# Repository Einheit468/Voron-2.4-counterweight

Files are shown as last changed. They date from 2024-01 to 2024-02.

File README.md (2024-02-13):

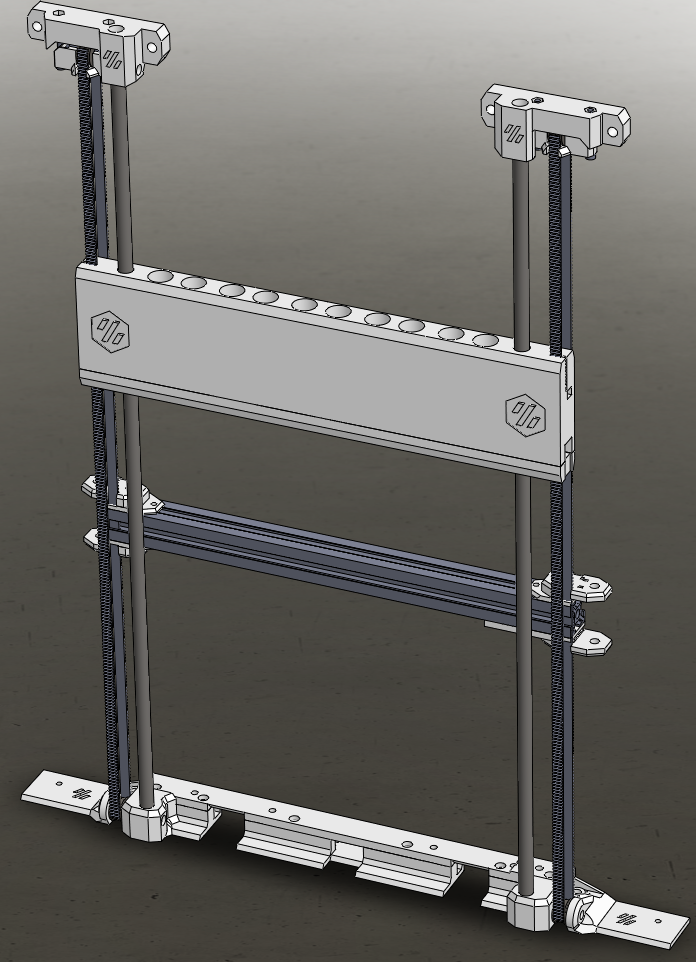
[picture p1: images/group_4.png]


The project is currently intended exclusively for __Voron 2.4 350mm__. <br>
The counterweight relieves the load on the rear Z stepper motors.<br>
Possible sagging of the gantry is also reduced.<br>

The disadvantage is that the acceleration force and braking force are increased.<br>
<br>
<br>

> [!WARNING]
> __I noticed that during input shaping the vibrations start to rattle due to the play in the counterweight bearing.
> Still looking for a solution to the problem.__

<br>
<br>
<br>
<br>

> [!WARNING]
> __The project is not yet fully completed.__ <br>
> - the building instructions are work-in-progess. <br>
> - some pictures are still old versions. <br>
> <br>
> But the parts and BOM are functional. <br>

> [!IMPORTANT]
> The __Z-cable chain__ must/should be exchanged for one of the narrower __X or Y cable chain__.

> [!IMPORTANT]
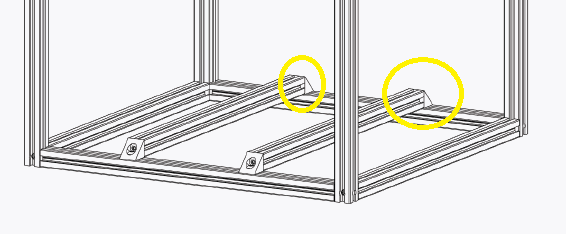
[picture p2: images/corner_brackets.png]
>  <br>
> The __corner brackets__ should also be attached to the ends of the heated bed bracket on the frame.

### Required Hardware:<br>
* List of Hardware: [BOM](/BOM.md)

### Build guide:<br>
* [Build](/Build.md)

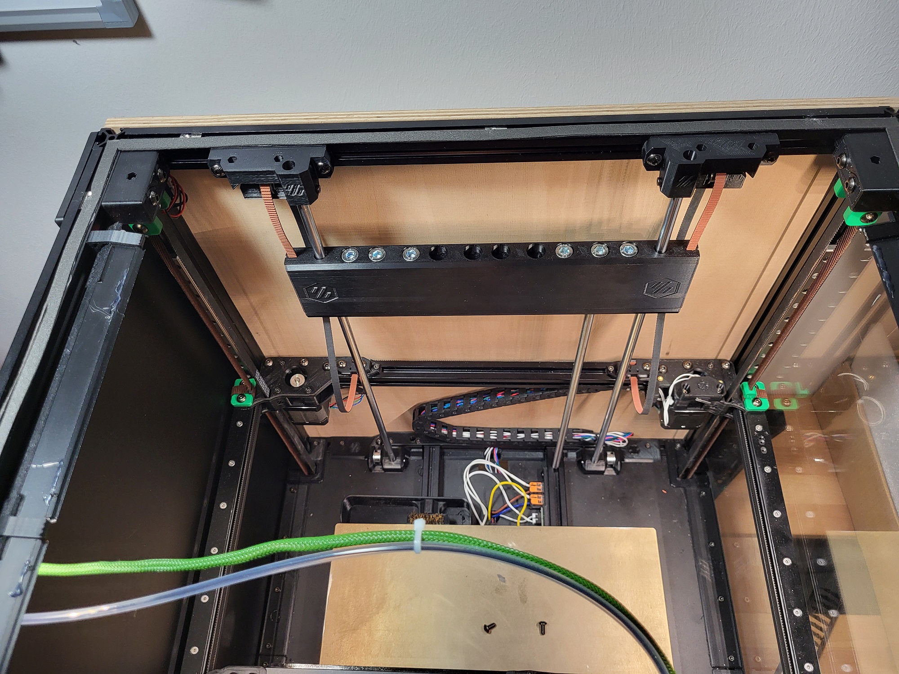
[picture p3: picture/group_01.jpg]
 <br>
_The weight is intentionally relaxed in the picture.
The lower strap is not mounted._

# Changelog

* 10.02.2024: modified the belt tension on  the gantry side. It wasn't aligned with the timing belts. <br> also added cable tie holders for timing belts and cables. <br>
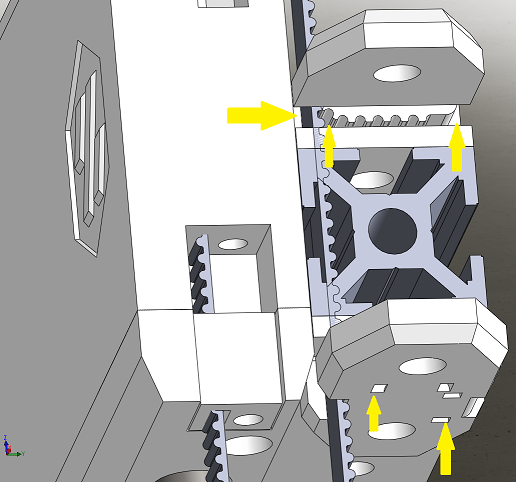
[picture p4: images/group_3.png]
  <br>
* 12.02.2024: Distance increased by 0.5mm between gantry and counterweight. <br> Because he sanded minimally.
<br>
<br>

# Special Thanks to
__spitzbirne32__

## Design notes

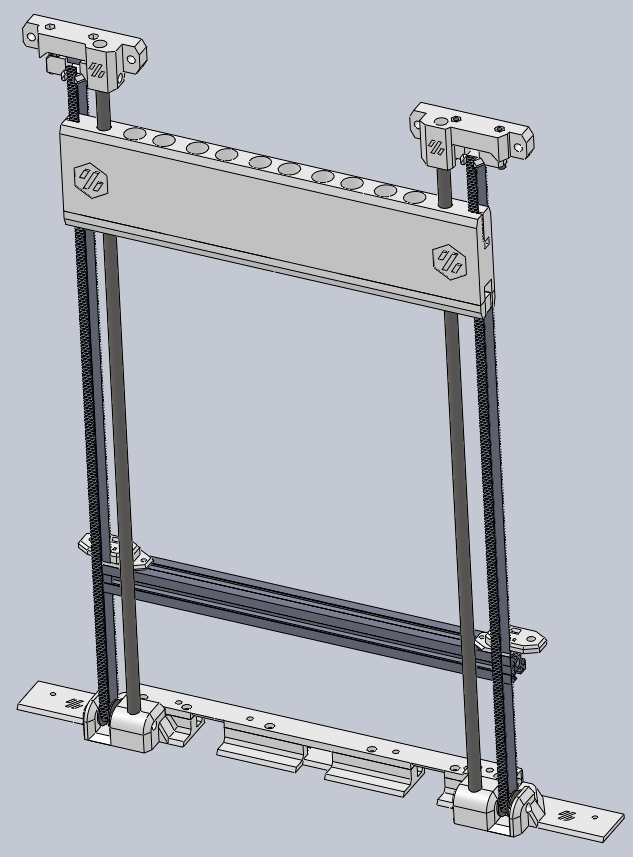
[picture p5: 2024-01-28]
images/group_1.png

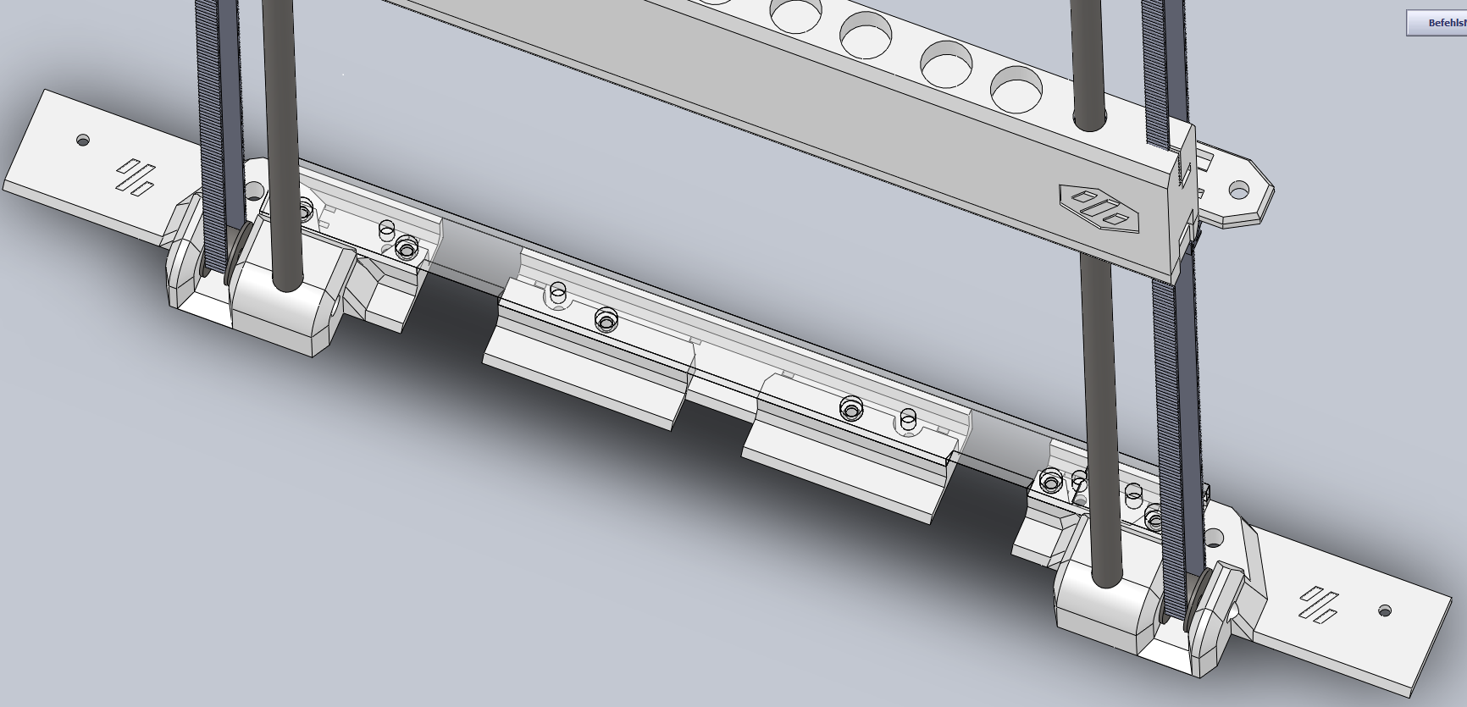
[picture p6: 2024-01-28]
images/beldholder_down_4.png

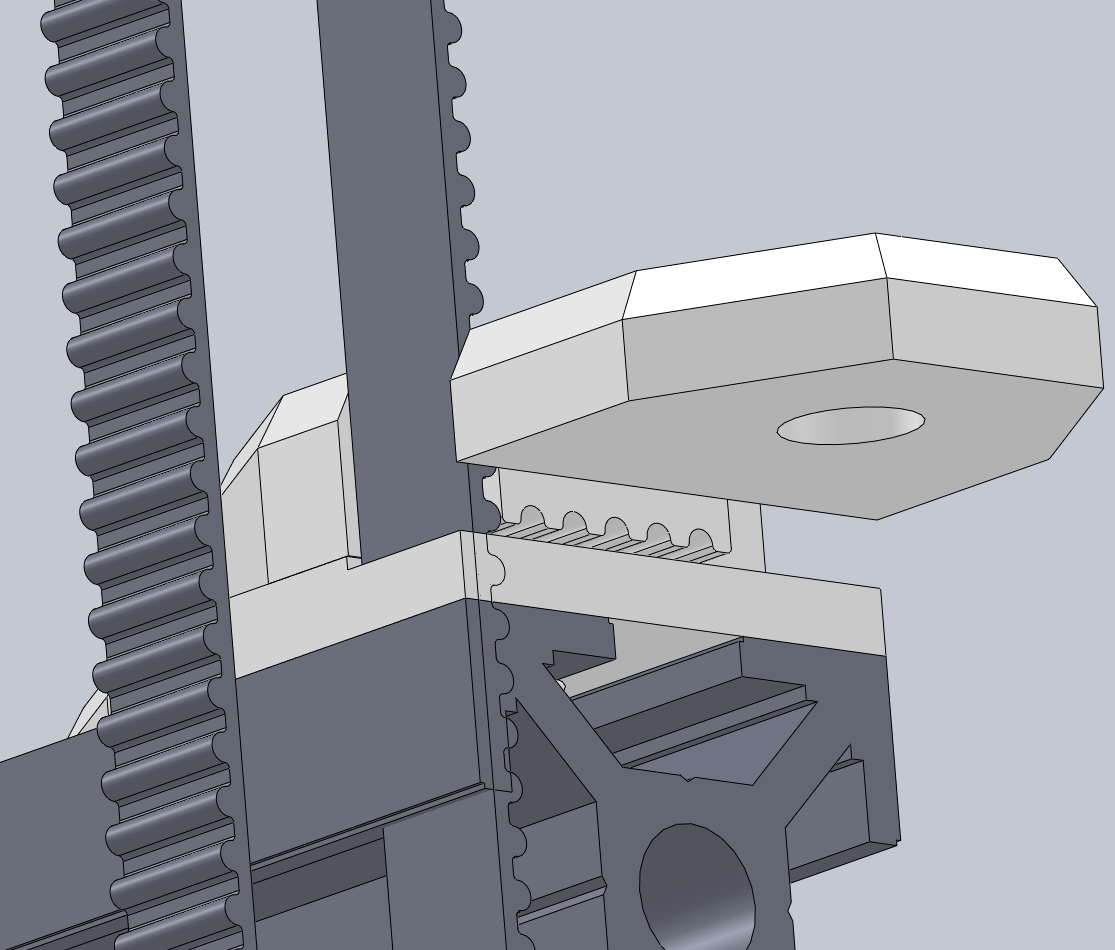
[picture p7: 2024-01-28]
images/gantry_2.png

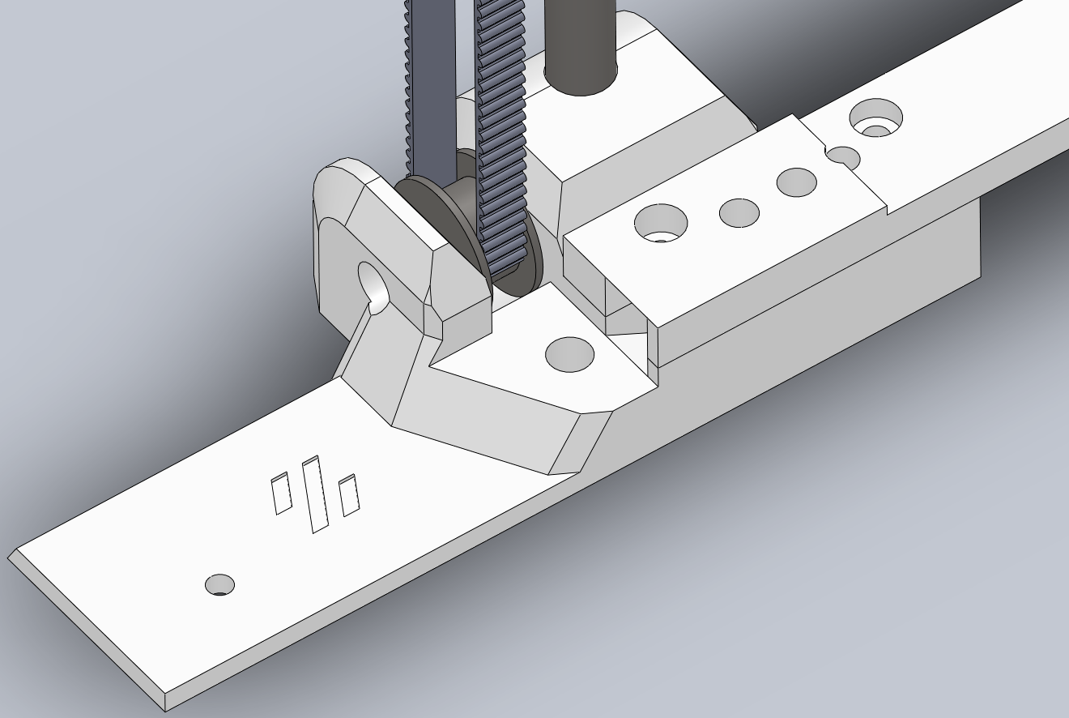
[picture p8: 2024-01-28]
images/beldholder_down_2.png

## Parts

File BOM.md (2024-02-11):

⬅ back to [Main Page](README.md)

__Table of contents__
- [Required Hardware](#Required-Hardware)
- [BOM beldholder_up](#beldholder_up)
- [BOM beldholder_down](#beldholder_down)
- [BOM counterweight](#counterweight)
- [BOM gantry](#gantry)

# Required Hardware
SHCS = normal screw/DIN912<br>
FHCS = flat-head cap screw/ISO10642<br>
BHCS = button head screw/ISO7380-1<br>

# beldholder_up
&uarr; [back to top](#top)<br>

| Qty | Item | Notes |
| --- | --- | --- |
| 2 | M3 Heatset Insert | Standard Voron spec: 5mm Outer Diameter x 4mm Length - for fixing the 8mm round rod |
| 2 | M3 x 6 SHCS or M3x10 SHCS | for fixing the 8mm round rod |
| 4 | M3x25 SHCS | |
| 4 | M3 Hexnut |  DIN934 - if possible self-locking but not a must |
| 4 | M5x16 BHCS or SHCS | |
| 2 | M5x20 BHCS or 5x18 PIN shaft | |
| 4 | M5 T-Nut | |
| 4 | F695-2RS Precision Bearing | |
| 4 | M5 Shim Ring | ~1mm thick |

# beldholder_down
&uarr; [back to top](#top)<br>

| Qty | Item | Notes |
| --- | --- | --- |
| 2 | M3 Heatset Insert | Standard Voron spec: 5mm Outer Diameter x 4mm Length - for fixing the 8mm round rod |
| 2 | M3 x 6 SHCS or M3x10 SHCS | for fixing the 8mm round rod |
| 8 | M3 Heatset Insert | Standard Voron spec: 5mm Outer Diameter x 4mm Length |
| 12  | M3x10 SHCS | |
| 6 | M3 T-Nut | |
| 2 | M5x16 BHCS | |
| 2 | M5x20 BHCS or 5x18 PIN shaft | |
| 2 | M5 T-Nut | |
| 2 | 8x500mm round rod | |
| X | small Zip Ties | |
| 2 | M3x6 FHCS | for fixing the cable chain |
| 4 | F695-2RS Precision Bearing | |
| 4 | M5 Shim Ring | ~1mm thick |

# counterweight
&uarr; [back to top](#top)<br>

| Qty | Item | Notes |
| --- | --- | --- |
| 6 | M3x12 SHCS or M3x16 SHCS | |
| 2 | M3x25 SHCS | |
| 6 | M3x5x4 Heatset Insert | |
| 10  | M8x60 SHCS | |
| 2 | M3 Hexnut | if possible self-locking but not a must |
| 60  | M10 Hexnut | | 
| 10  | M8 Hexnut | |
| 2 | 8mm Linear bearing |  45mm long |

# gantry
&uarr; [back to top](#top)<br>

| Qty | Item | Notes |
| --- | --- | --- |
| 2 | M3 Heatset Insert | Standard Voron spec: 5mm Outer Diameter x 4mm Length - for fixing the cable chain |
| 2 | M3x6 FHCS | for fixing the cable chain |
| 4 | M3x10 BHCS | |
| 4 | M5x16 BHCS | |
| 4 | M3 T-Nut | |
| 4 | M5 T-Nut | |
| 2 | GT2 6mm beld | 470mm long (for up-side) |
| 2 | GT2 6mm beld | 506mm long (for down-side) |
| 1 | Cable chain | ~500mm long (with endparts) its 26 parts with 2 endparts; out dimensions 17wide x 14,5 high |

⬅ back to [Main Page](README.md)

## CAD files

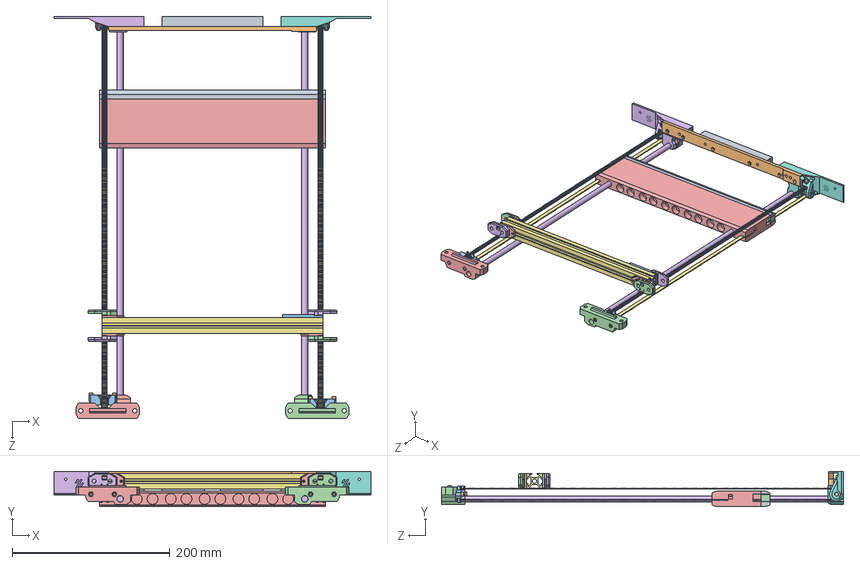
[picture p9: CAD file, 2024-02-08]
CAD/counterweight_groupe.SLDASM
401.8 x 44.8 x 510.0 mm
counterweight_cover
2x bearing_space_small x 2
Rotex 8mm Lager x 3
2x beld_tensioner x 2
counterweight_center_v2
Eisenstab_8x500 x 2
beld_8mm_500mm x 4
F695_2RS_Bearing x 8
M5x20_screw x 2
M3x25 x 4
beldholder_up_iddler_V2 x 2
beldholder_up_right_mount_V2
beldholder_up_left_mount_V2
beldholder_down_left_V3
5x18_Bolzen x 2
beldholder_down_right_V3
cable_canal_down_middle
cable_towing_support
beldholder_flexible_button_cable_drag
2x beld_tensioner_gantry_a x 2
3x beldholder_flexible_button x 3
2x beld_tensioner_gantry_b x 2
Aluprofil_20x20x490

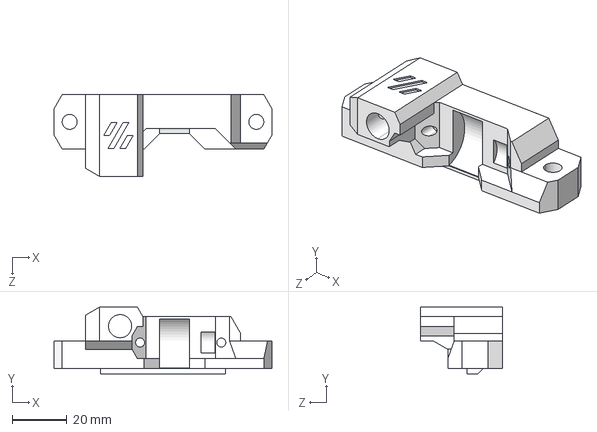
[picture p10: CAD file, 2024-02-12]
CAD/bedholder_up/beldholder_up_right_mount_V2.STEP
80.0 x 24.5 x 30.0 mm

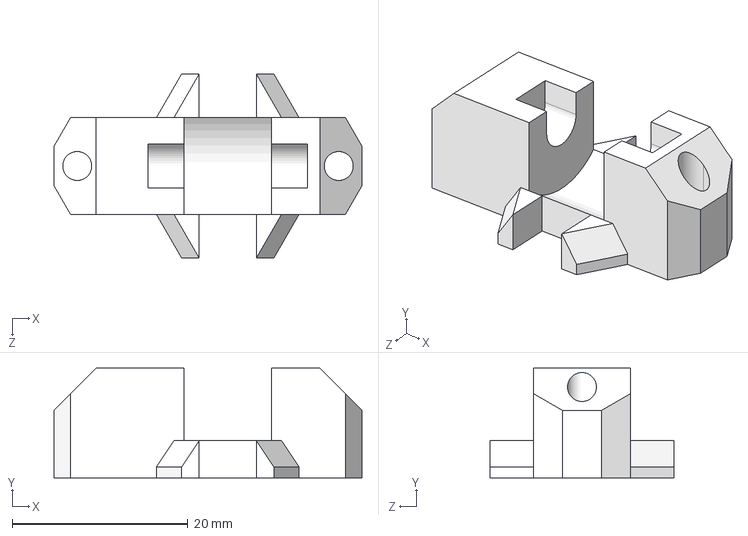
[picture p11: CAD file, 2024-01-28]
CAD/bedholder_up/optional/beldholder_up_iddler_V2_PIN_Mod.STEP
35.1 x 12.5 x 21.0 mm

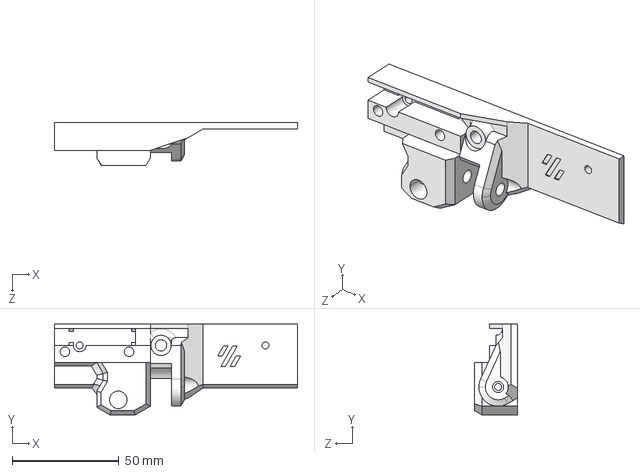
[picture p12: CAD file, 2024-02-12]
CAD/beldholder_down/beldholder_down_right_V3.STEP
113.8 x 42.6 x 20.0 mm

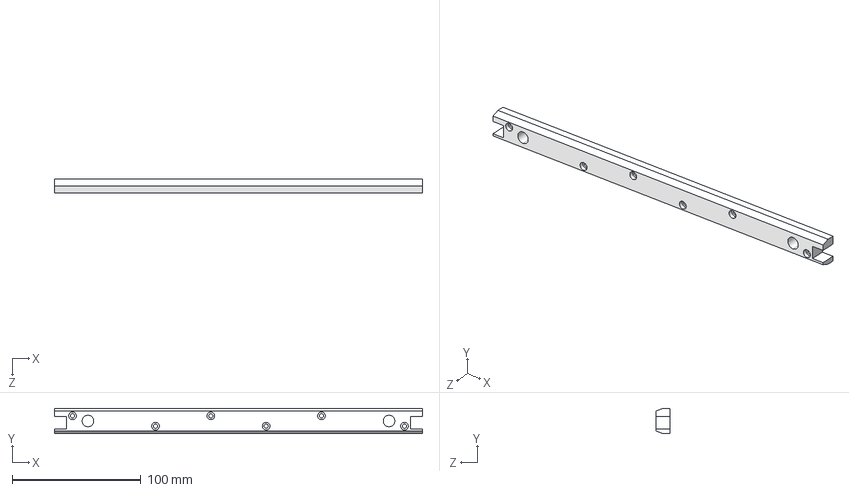
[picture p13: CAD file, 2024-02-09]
CAD/counterweight/counterweight_cover.STEP
286.0 x 19.6 x 11.0 mm

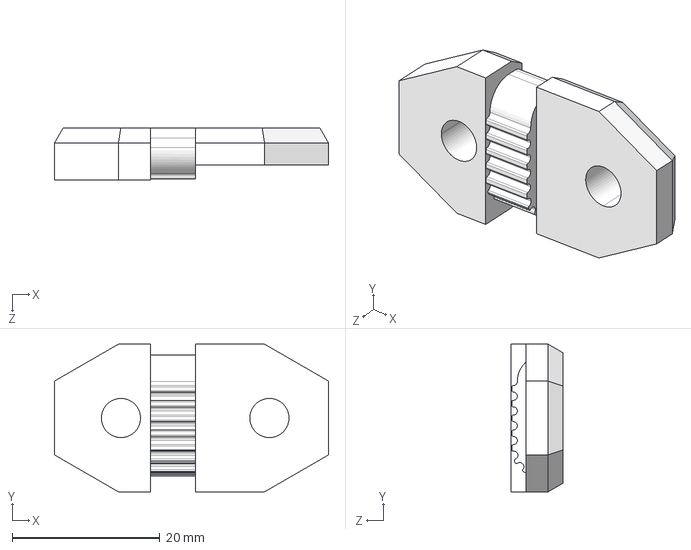
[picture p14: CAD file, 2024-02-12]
CAD/gantry/2x beld_tensioner_gantry_b_V3.STEP
37.1 x 20.0 x 7.00 mm

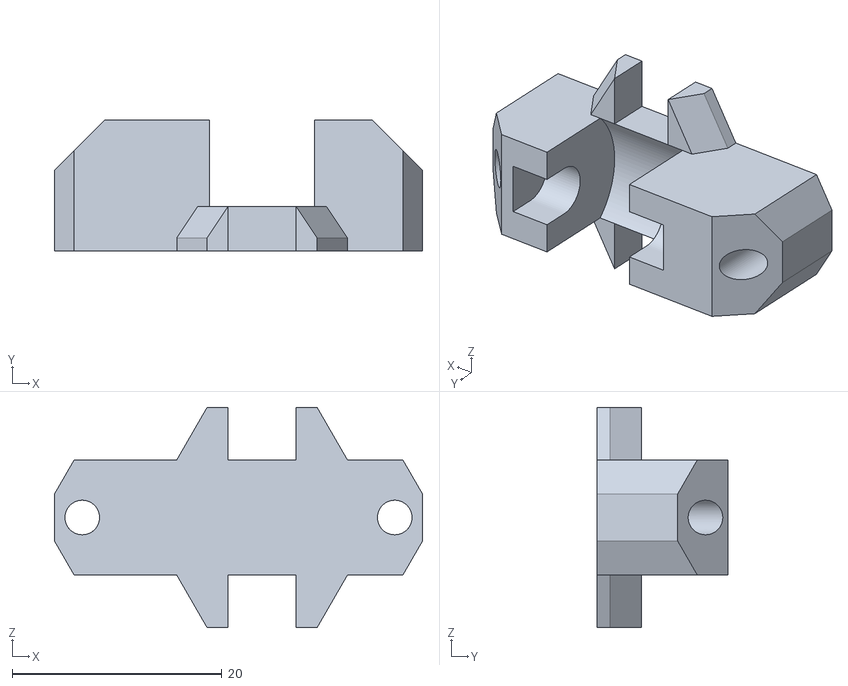
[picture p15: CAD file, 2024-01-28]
STLs/beldholder_up/optional/beldholder_up_iddler_V2_PIN_Mod.STL
35.1 x 12.5 x 21.0

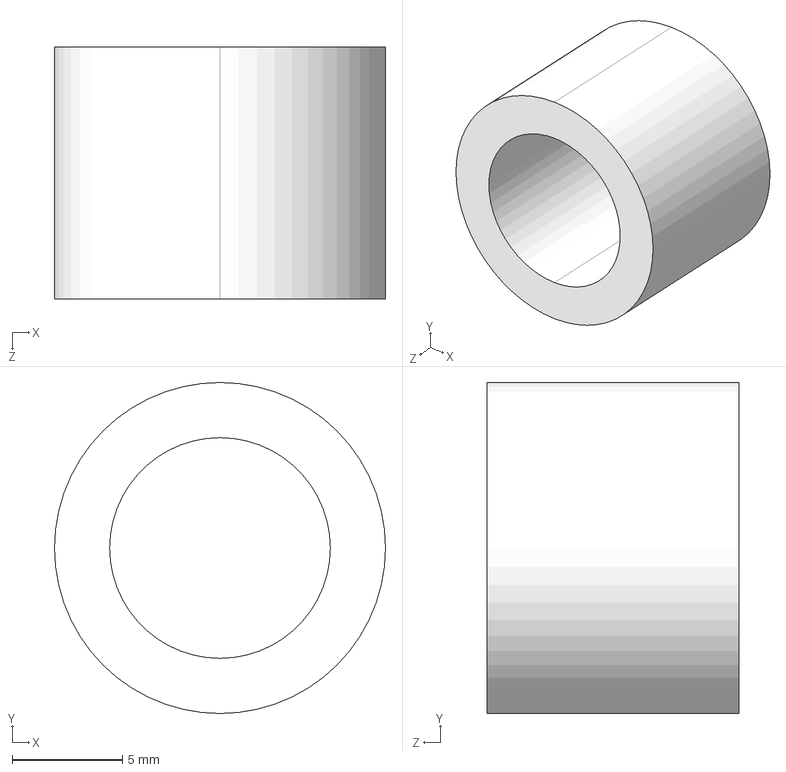
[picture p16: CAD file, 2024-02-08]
CAD/counterweight/2x bearing_space_small.STEP
15.0 x 15.0 x 11.4 mm

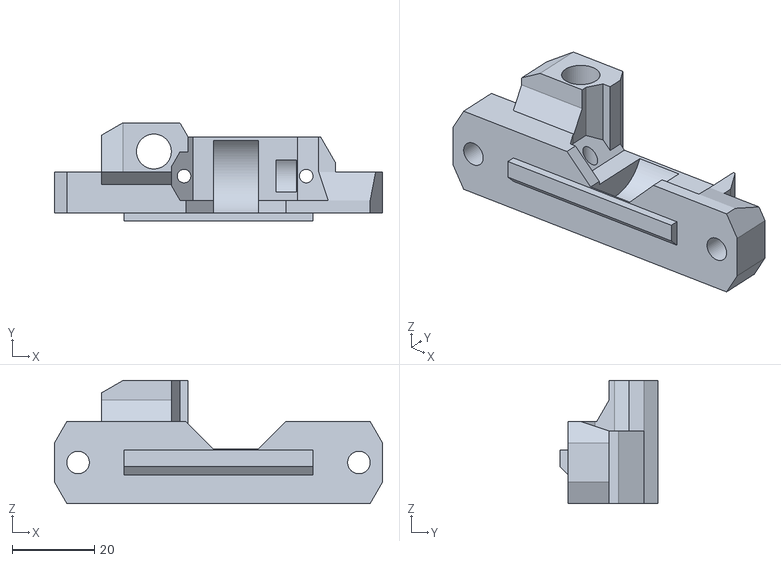
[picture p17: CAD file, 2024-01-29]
STLs/beldholder_up/beldholder_up_right_mount_V2.STL
80.0 x 24.0 x 30.0

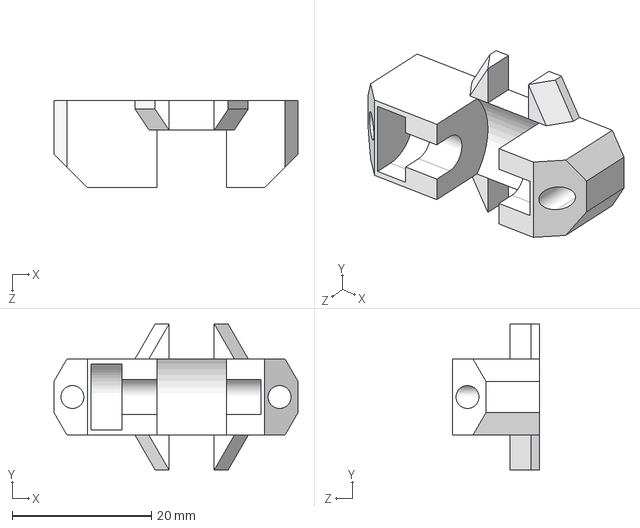
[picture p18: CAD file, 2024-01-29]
CAD/bedholder_up/beldholder_up_iddler_V2.STEP
35.1 x 21.0 x 12.5 mm

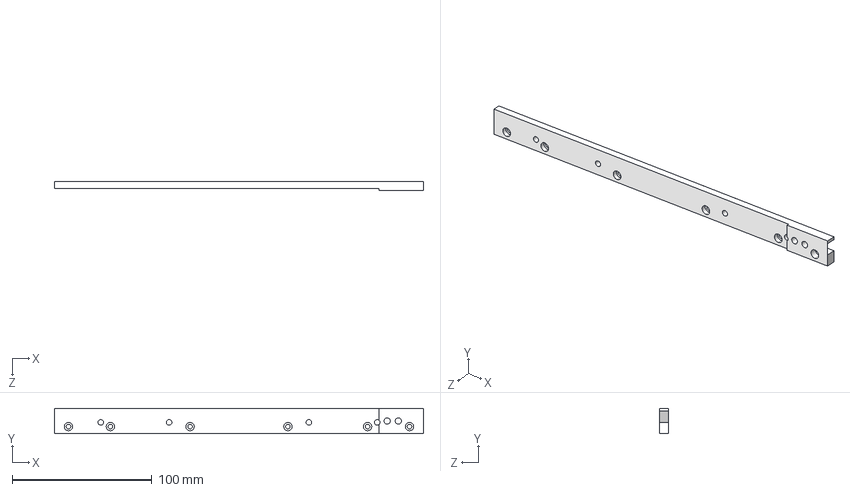
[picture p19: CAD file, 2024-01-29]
CAD/beldholder_down/cable_towing_support.STEP
264.0 x 18.0 x 6.50 mm

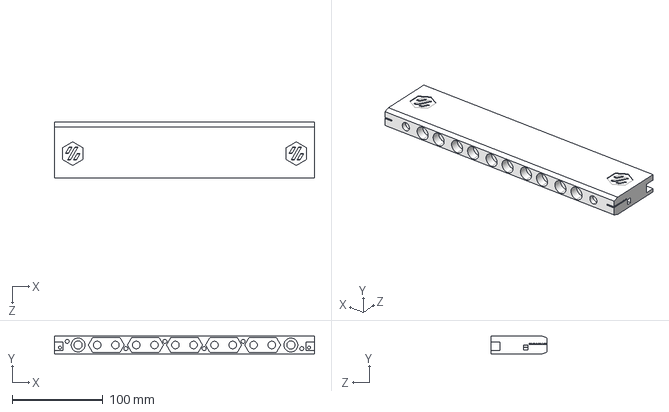
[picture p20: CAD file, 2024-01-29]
CAD/counterweight/counterweight_center_v2.STEP
286.0 x 19.6 x 62.0 mm

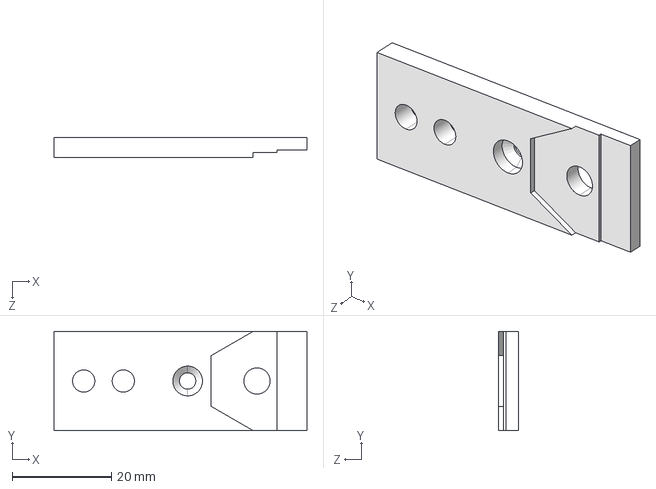
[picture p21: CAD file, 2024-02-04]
CAD/gantry/beldholder_flexible_button_cable_drag.STEP
51.1 x 20.0 x 4.00 mm

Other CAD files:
STLs/beldholder_up/beldholder_up_left_mount_V2.STL
CAD/bedholder_up/beldholder_up_left_mount_V2.STEP
CAD/beldholder_down/beldholder_down_left_V3.STEP
CAD/gantry/2x beld_tensioner_gantry_a_V3.STEP
STLs/beldholder_up/beldholder_up_iddler_V2.STL
CAD/bedholder_up/beldholder_up_iddler_V2.SLDPRT
CAD/bedholder_up/beldholder_up_left_mount_V2.SLDPRT
CAD/bedholder_up/beldholder_up_right_mount_V2.SLDPRT
CAD/bedholder_up/optional/beldholder_up_iddler_V2_PIN_Mod.SLDPRT
CAD/beldholder_down/beldholder_down_left_V3.SLDPRT
CAD/beldholder_down/beldholder_down_right_V3.SLDPRT
CAD/beldholder_down/cable_canal_down_middle.SLDPRT
CAD/beldholder_down/cable_canal_down_middle.STEP
CAD/beldholder_down/cable_towing_support.SLDPRT
CAD/counterweight/2x bearing_space_small.SLDPRT
CAD/counterweight/2x beld_tensioner.SLDPRT
CAD/counterweight/2x beld_tensioner.STEP
CAD/counterweight/counterweight_center_v2.SLDPRT
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

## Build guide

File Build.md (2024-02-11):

⬅ back to [Main Page](README.md)

__Table of contents__
- [01 Printing](#01-Printing)
- [02 modification AB-Gantry](#02-modification-AB-Gantry)
- [03 beldholder down](#03-beldholder-down)
- [04 counterweight](#04-counterweight)
- [05 beldholder up](#05-beldholder-up)
- [06 hang and tension](#06-hang-and-tension)

> [!WARNING]
> The instructions refer to converting a built Voron, with a Can-Bus Toolhead.<br>
> Because the Z-cable chain needs to be replaced with the thinner ones.<br>
> Don't be surprised, the pictures are still old, the STL files are newer and correct.<br>

# 01 Printing
Printing the Parts with the normal settings of the Voron build.
- Material: ABS
- Layer heigh: 0.2mm
- Extrusion width: 0.4
- Infill: Grid, Gyroid, Honeycomb, Triangle or Cubic
- Infill Percentage: Recommended: 40%
- Wall Count: Recommended: 4
- Solide Top/Bottom Layer: Recommended: 5

# 02 modification AB-Gantry
&uarr; [back to top](#top)<br>

* For better assembly, move or push the gantry approximately 2/3 upwards.<br>
* Completely remove the existing Z chain.<br>
* Insert 2x M3 Heat Set Inserts for the cable chain attachment into the "beldholder_flexible_button_cable_drag".<br>

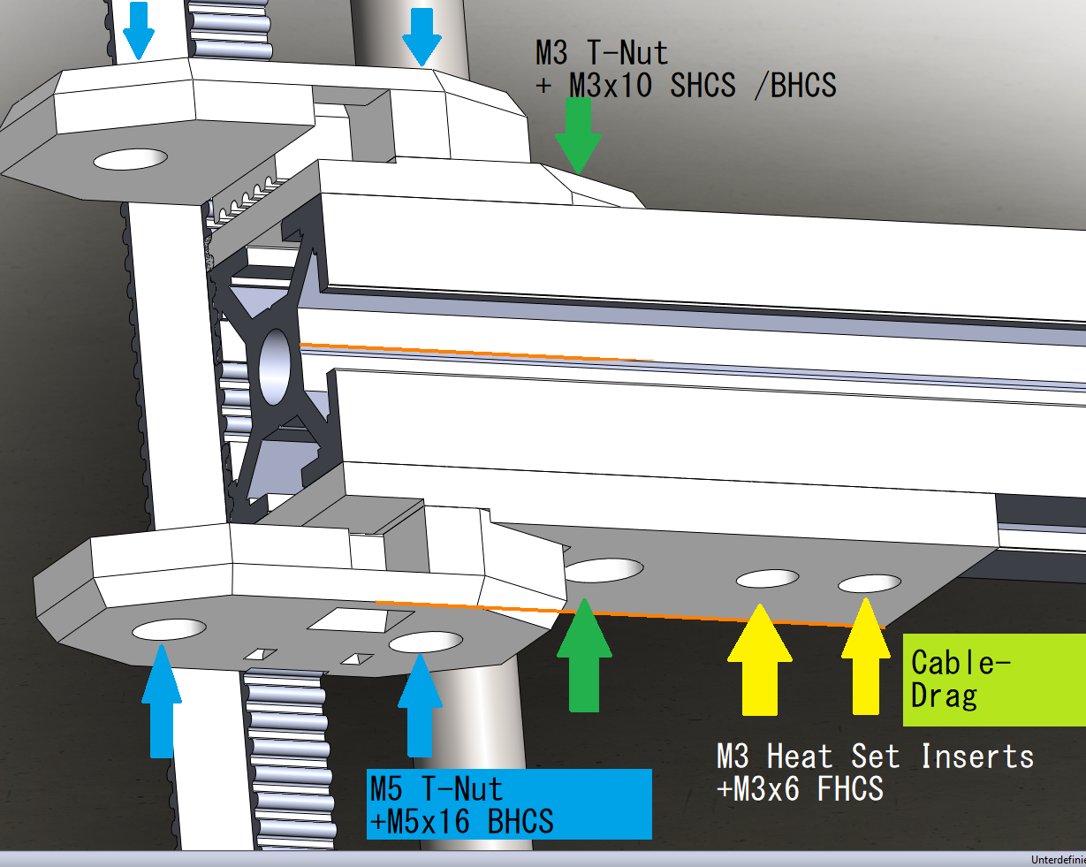
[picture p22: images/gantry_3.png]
<br>

_(The image is without AB_Drive_Units, it starts where the profile ends.)_
<br>
<p>
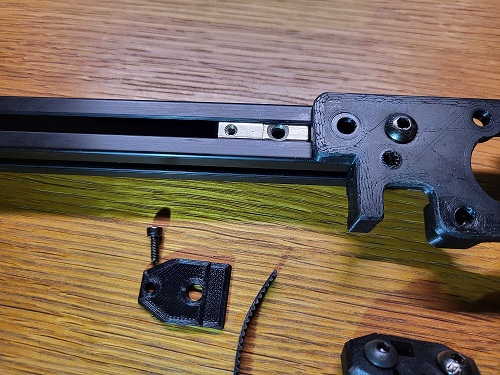
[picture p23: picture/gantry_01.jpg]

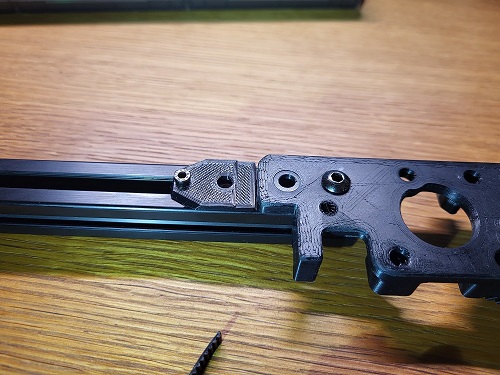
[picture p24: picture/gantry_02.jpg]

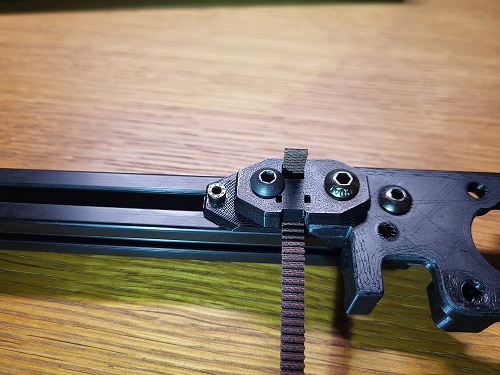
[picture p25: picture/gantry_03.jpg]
<br>
</p> <br>

* Attach the button parts with stops to the original "AB_Drive_Units".<br>
* To do this, place M3 and M5 T-slots in the aluminum profile.<br>
* And fasten with the M3 screws provided.<br>
* cut the down belts to 506mm leng.
* cut the up belts to 470mm leng.
* Then attach the timing belts to the holders with the M5x16 screws.<br>
* Fill the cables with the narrower cable tow that you have from the X or Y tow, for example, as the Z tow. (Reason: The original Z-cable tow is wider than the aluminum profile)<br>

* Attach the cable tow to the top with the bracket.<br>
* Please note that the cable for the left motor branches off into the aluminum profile before it is attached.<br>

* Attention, the motor cable of the left motor is tight.<br>

# 03 beldholder down
&uarr; [back to top](#top)<br>
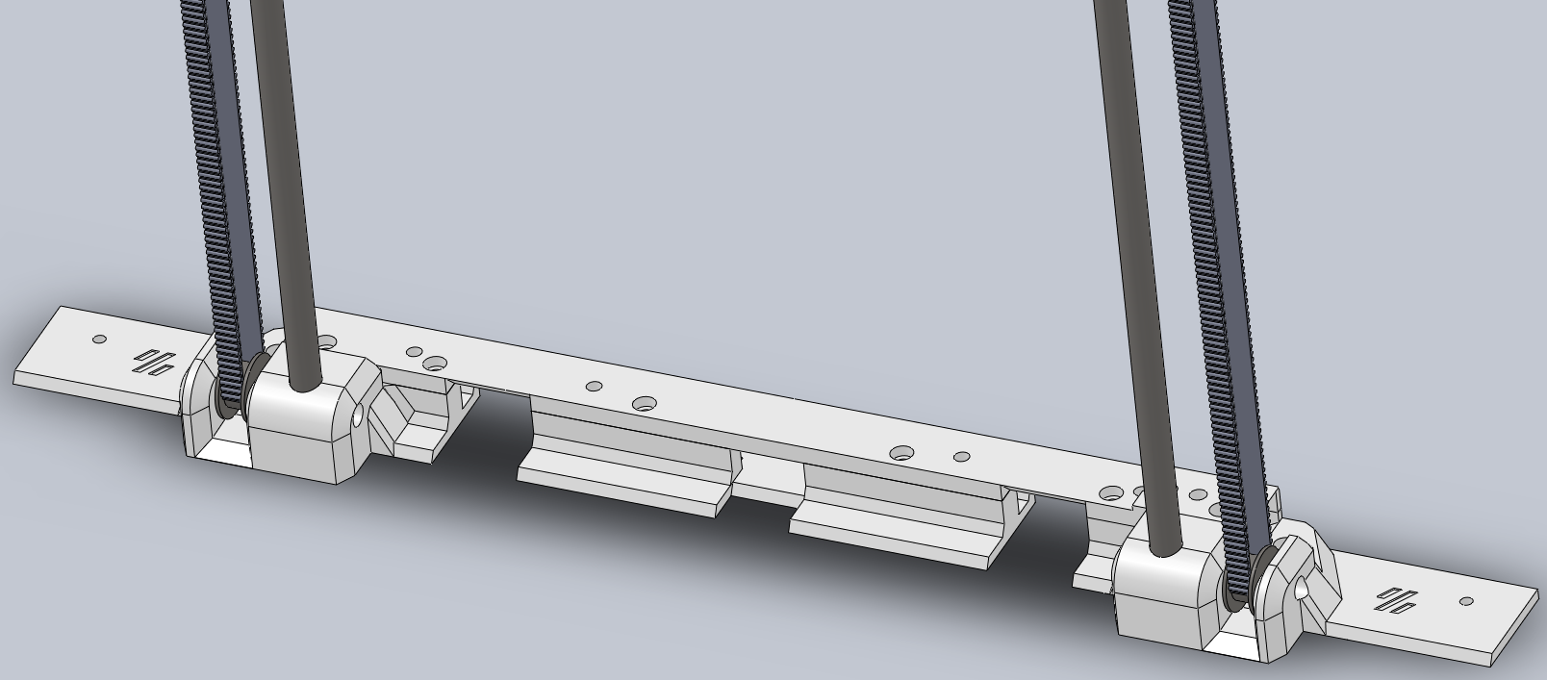
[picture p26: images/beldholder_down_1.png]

<br>
<p>
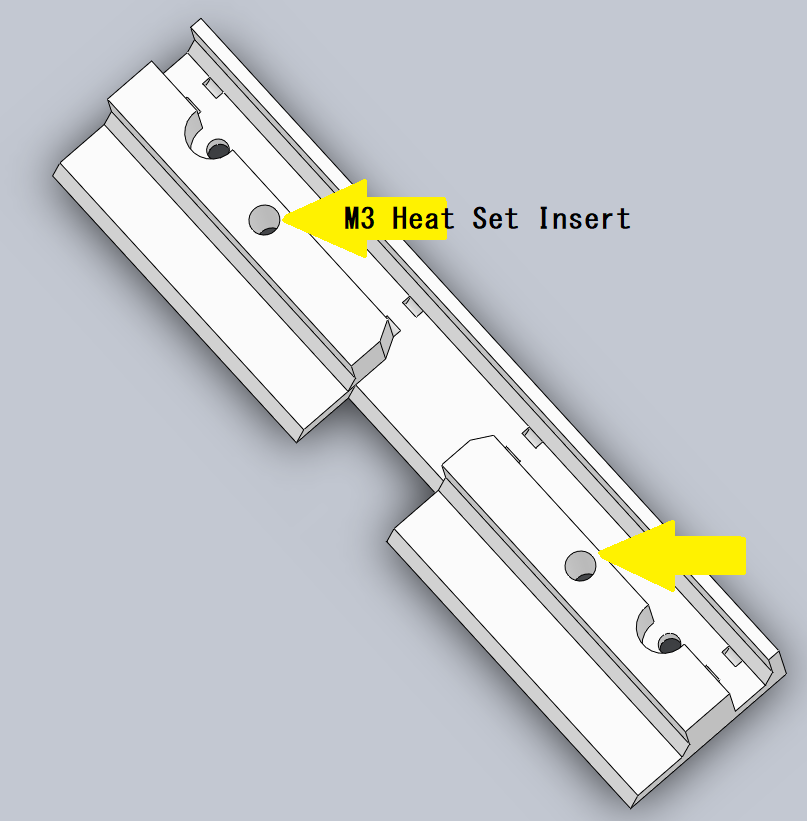
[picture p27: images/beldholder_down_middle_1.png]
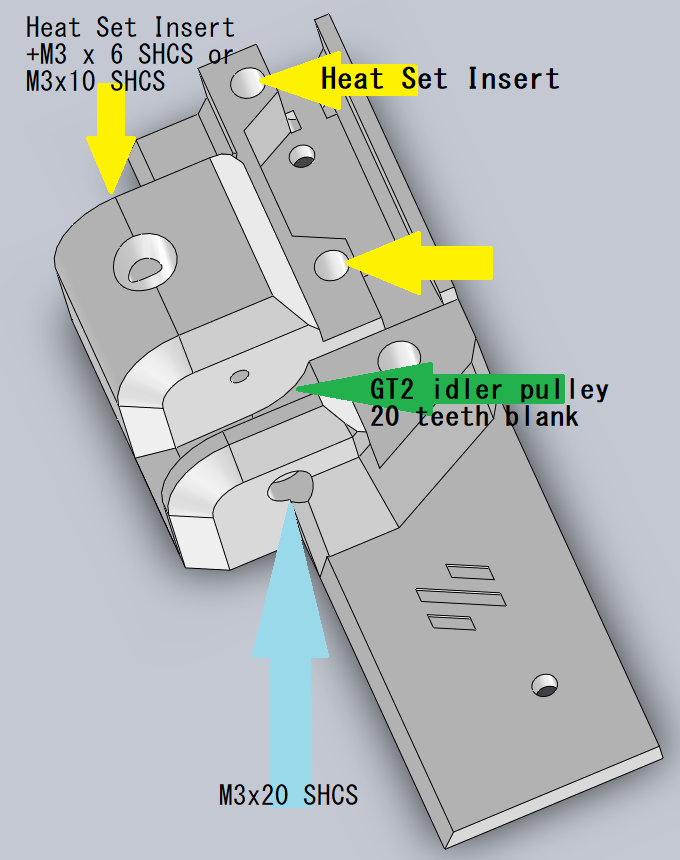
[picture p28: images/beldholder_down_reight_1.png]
 
<p/>
  
* Insert M3 Heat Set Inserts<br>
* Please do the same on the left side as on the right side.<br>
<br>

* Place the "T-Nut_Tool" on the aluminum profile and insert the T-Nut. <br> The side of the label is the side where the thread is located.<br>
* remove the "T-Nut_Tool"<br>
* bring the printparts to the aluminum profile<br>
<br>
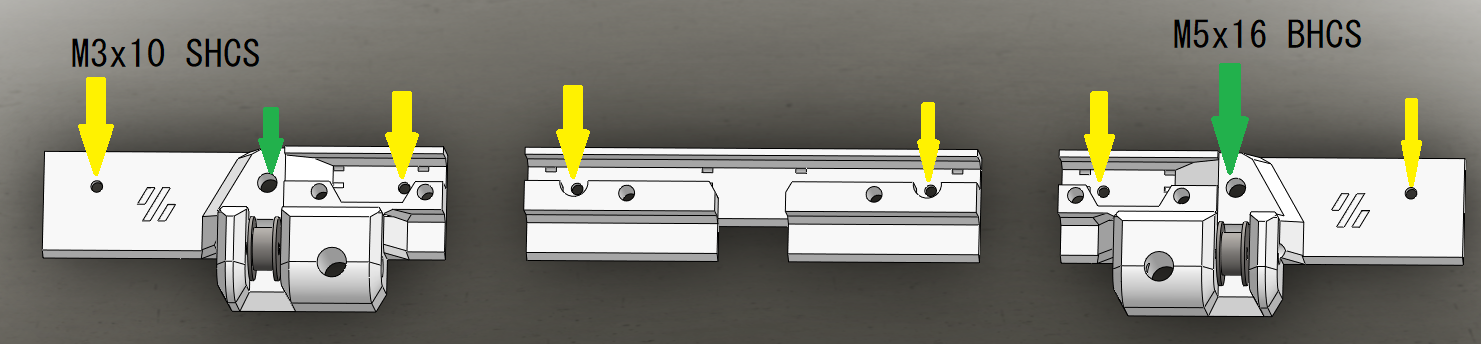
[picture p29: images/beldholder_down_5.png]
 <br>

* insert the screws into the holes provided on the T-nut. But only tighten the screws loosely.<br>
<br>
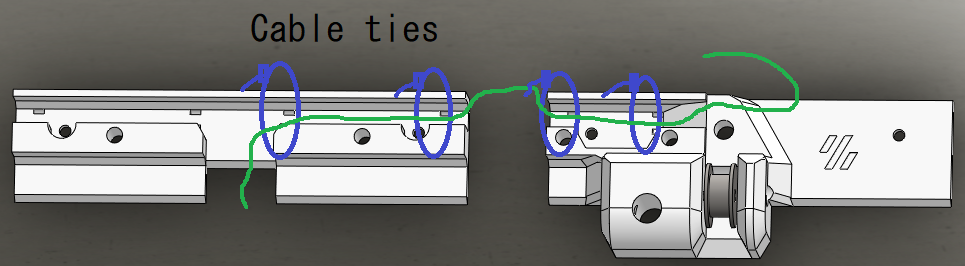
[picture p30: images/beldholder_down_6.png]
 <br>
  
* Lay the cables for the tow as shown. <br> 
* And do not tighten the cable ties completely. <br> The cable should still be able to move back and forth. <br> The cable ties are initially used to ensure that no cables are crushed. <br>
* Cut off the ends of the cable ties. <br> 
<br>
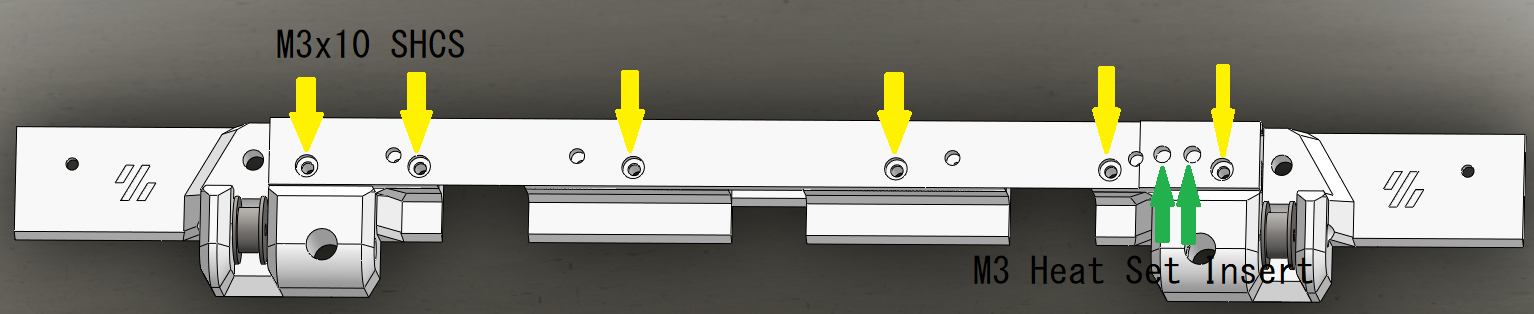
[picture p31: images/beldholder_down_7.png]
 <br>

* Set up the "cable_towing_support"<br>
* align all parts and tighten the screws for the "cable_towing_support" first<br>
* then attach all screws through the holes to the T-slot nuts<br>
* Attach the cable trailing end to the support.

# 04 counterweight
&uarr; [back to top](#top)<br>
<p>
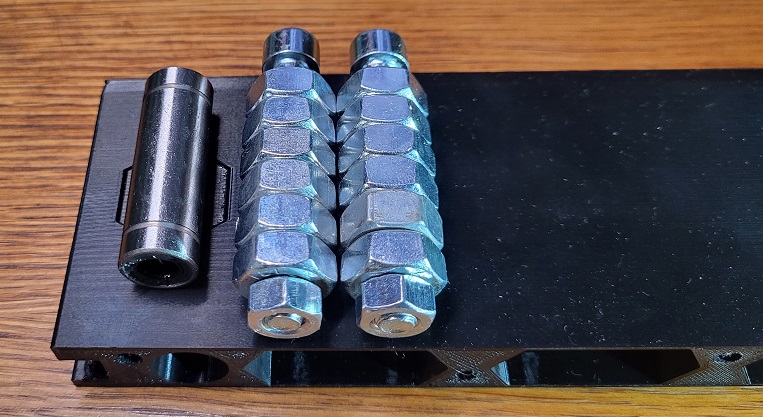
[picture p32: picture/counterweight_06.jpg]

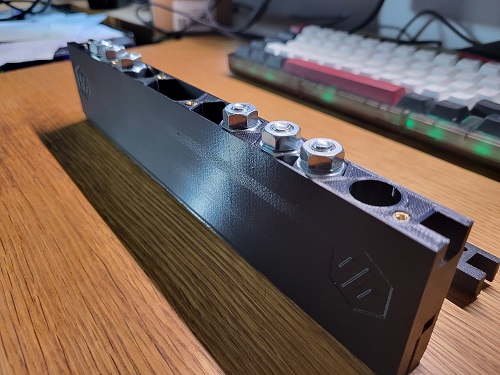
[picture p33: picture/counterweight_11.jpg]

<p/> <br>
  
* Pierce the holes in the support with the M8 screws.<br>
* Insert 6x M10 nuts into each screw and then tighten with the M8 nut. (But be careful, it's just plastic.)<br>
* Put as much weight as you think of. (I currently have 8 screws in it.) <br>
* insert the 2 longitudinal bearings into the recess.<br>
* also put the 2 fits behind it.<br>
<p>
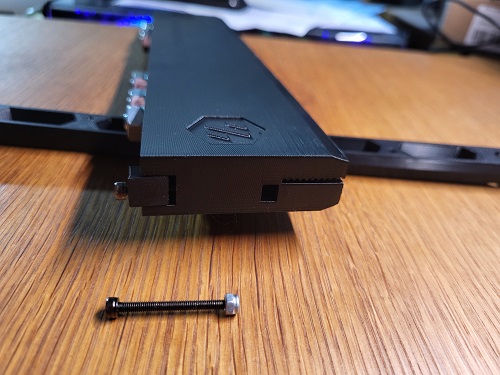
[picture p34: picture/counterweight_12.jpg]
 
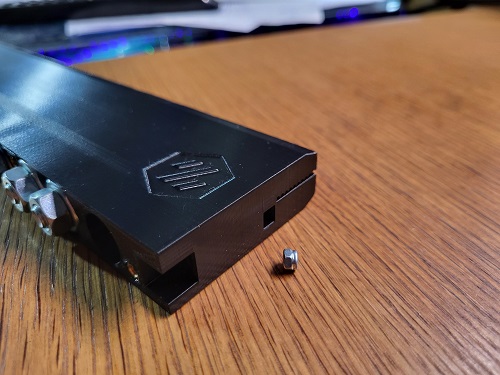
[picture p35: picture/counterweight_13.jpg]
 
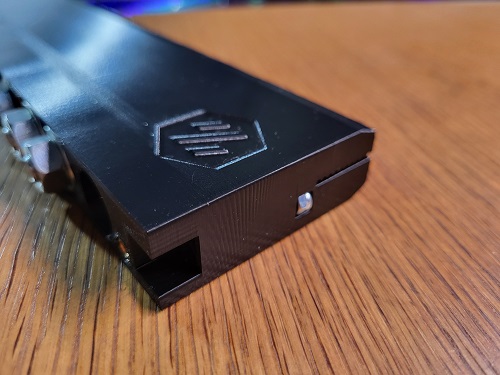
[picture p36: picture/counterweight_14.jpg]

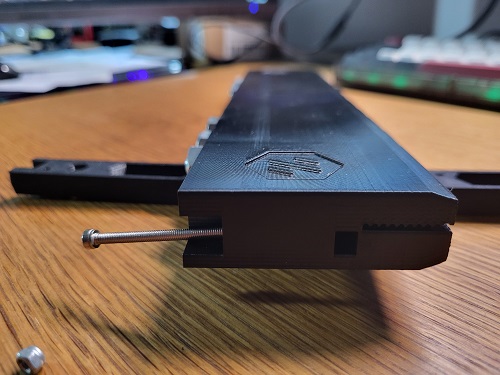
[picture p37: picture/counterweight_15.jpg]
<br>
<p/>

Don't forget to attach the M3 Heat Set Inserts to the bottom for the lid.

# 05 beldholder up
&uarr; [back to top](#top)<br>
<p>
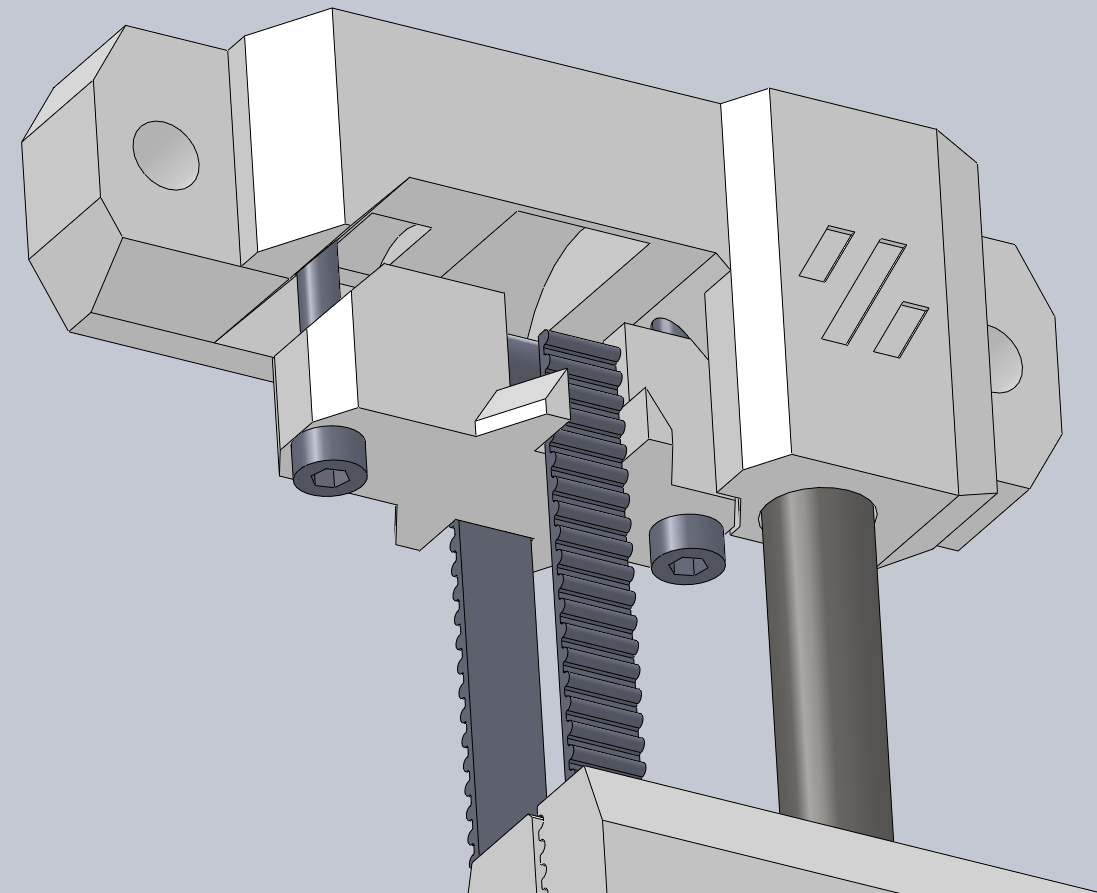
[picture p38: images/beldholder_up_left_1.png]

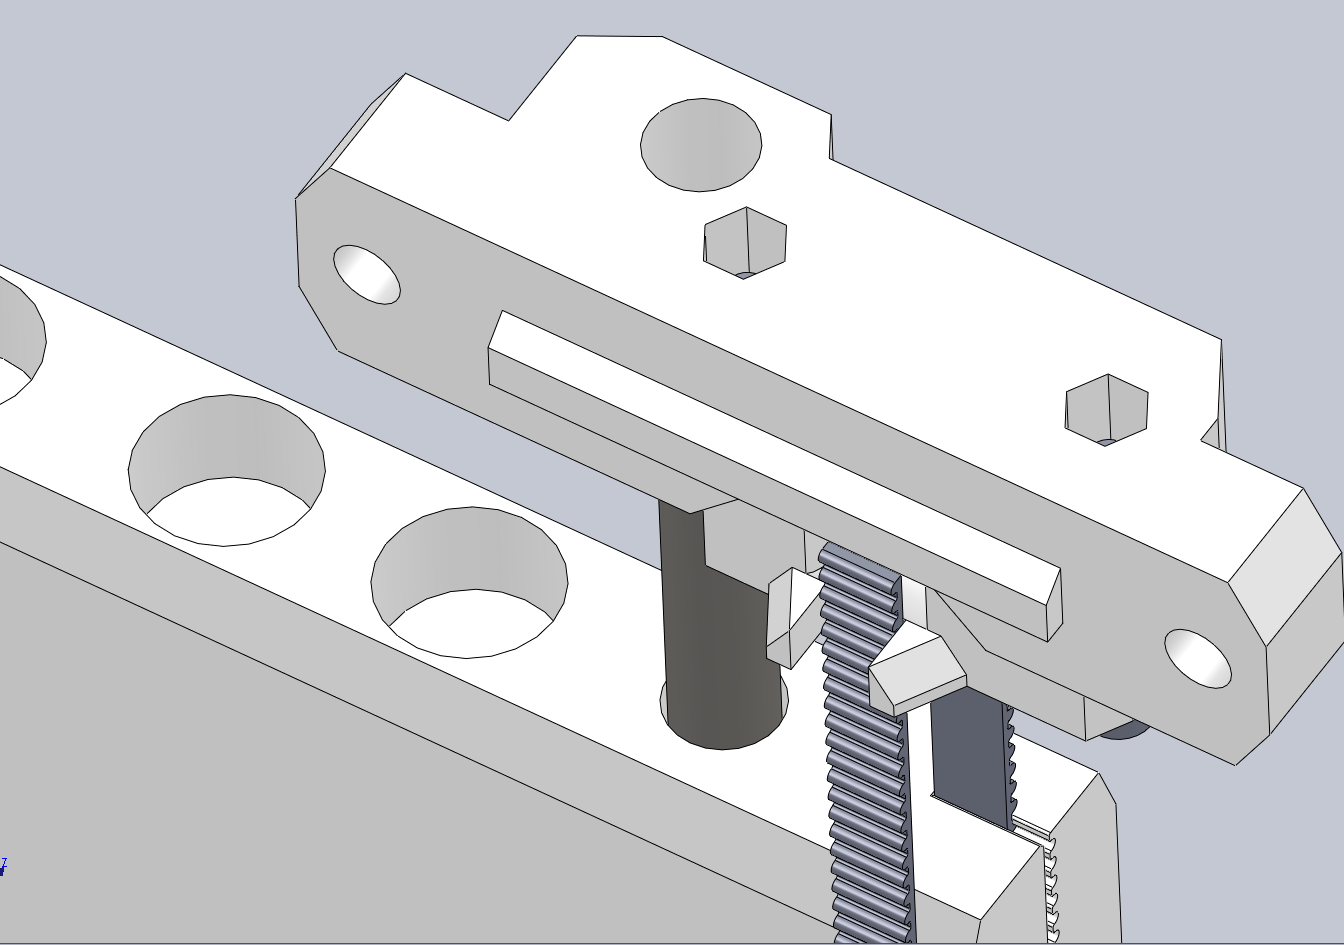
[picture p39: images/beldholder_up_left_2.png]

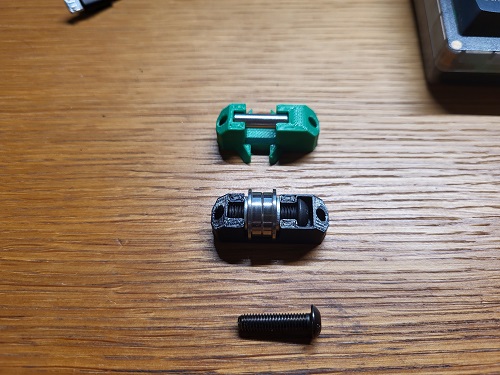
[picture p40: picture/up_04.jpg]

<p/> <br>
coming soon...

# 06 hang and tension
&uarr; [back to top](#top)<br>
coming soon...<br><br>

⬅ back to [Main Page](README.md)

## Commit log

2024-01-28 Update and rename CAD/bedholder_up/beldholder_up_iddler_V2_PIN_Mod.STEP to CAD/bedholder_up/optional/beldholder_up_iddler_V2_PIN_Mod.STEP
    [beldholder_up_iddler_V2_PIN_Mod.STEP]
2024-02-04 Rename CAD/2x beld_tensioner_gantry_a.SLDPRT to CAD/gantry/2x beld_tensioner_gantry_a.SLDPRT
    [2x beld_tensioner_gantry_a.SLDPRT]
2024-02-10 Update BOM.md
    spelling corrected
